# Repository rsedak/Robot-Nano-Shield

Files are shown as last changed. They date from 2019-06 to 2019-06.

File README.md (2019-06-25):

Introduction
============

Robot Nano Shield is Arduino Nano based shield for robots with dimentions compatibile with Lego(TM) liftarms.
For voltage stability L78S05CV Positive-Voltage regulator is used, and for power supply you can use two Li-Ion 18650 batteries.
During programming please keep in mind next design rules:
- D0-D1 — reserved for Bluetooth module (TX have onboard resistor voltage devider for HC-06 module)
- D2-D7 — reserved for H-bridge module (aka. L298N Dual H Bridge)
- D8 — reserved for servo motor
- D9-11 — reserved for RGB LED with onboard resistors
- D12-D13 — reserved for ultrasonic sensor HC-SR04
- A4-A5 — reserved for I2C communication with onboard pull-up resistors

Notice
------
Bluetooth module has to be disconnected during uploading a program to the Arduino Nano. 

Contributors
------------
- Petar Jurković had an idea for the shield with dimensions and features.
- Ines Sedak drew PCB back side picture.
- Robert Sedak did all design.

Application
-----------
Petar Jurković made video with Robot Nano Shield application in his robot:
Shield application (http://www.youtube.com/watch?v=B9CNlWZxvcw "Shield application")

Petar Jurković's Robot Nano Shield application
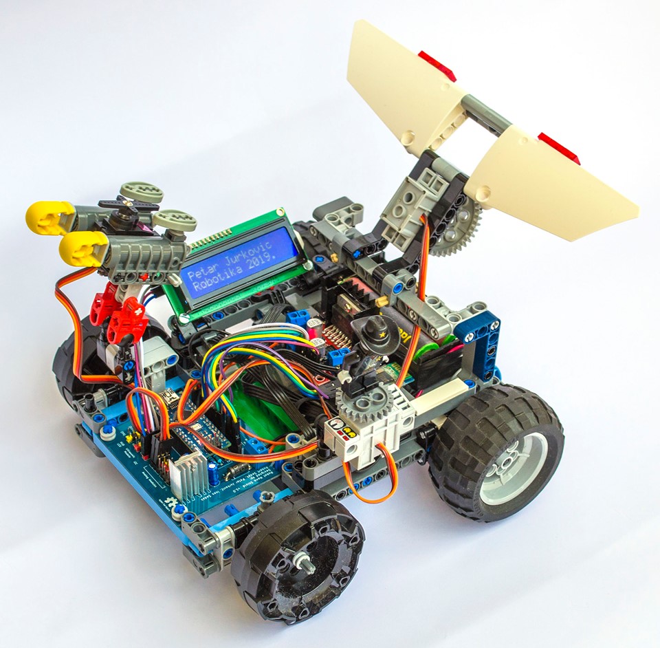
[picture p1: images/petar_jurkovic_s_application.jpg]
Robot Nano Shield Application
 

Bill Of Materials
-----------------
  
- 1 ea., PCB from [PCBway.com](https://www.pcbway.com/project/shareproject/Robot_Nano_Shield.html)
- 2 ea., 560 ohm 1/4W 1% Resistor (R2, R3)
- 2 ea., 1K ohm 1/4W 1% Resistor (R1, R4)
- 1 ea., 2K ohm 1/4W 1% Resistor (R5)
- 2 ea., 10K ohm 1/4W 1% Resistor (R6, R7)
- 1 ea., RGB LED 5mm common Katode (D1)
- 1 ea., 1N5400 Rectifier Diode (D2)
- 1 ea., L78S05CV Positive-Voltage regulator (U1)
- 1 ea., 10uF/25V Radial Aluminium Electrolytic Capacitor (C1)
- 1 ea., 220uF/10V Radial Aluminium Electrolytic Capacitor (C2)
- 1 ea., 2 Pin Plug-In Screw Terminal Block Connector 5.08mm Pitch
- 1 ea., 1x40Pin 2.54mm Straight Pin Header - Yellow
- 1 ea., 1x40Pin 2.54mm Straight Pin Header - Red
- 1 ea., 1x40Pin 2.54mm Straight Pin Header - Black
- 1 ea., 1x4 pin 2.54mm Socket Connector
- 2 ea., 1x15 pin 2.54mm Socket Connector
- 1 ea., Aluminum Heatsink Heat Sink with Screw Sets TO-220 Transistor 20×15×10mm

Design Files
------------
This project is designed using Open Source [KiCad](http://kicad-pcb.org/). Design files are located in the [design_files](design_files/) folder.  You can see the [schematic](images/robot_nano_shield_sch.png).

Firmware
--------
This project can be programed using the Open Source [Arduino](https://www.arduino.cc/).

Assembly Instructions
---------------------
TBD

License
-------
[Attribution-ShareAlike 3.0 United States (CC BY-SA 3.0 US)](https://creativecommons.org/licenses/by-sa/3.0/us/)

You are free to:
- Share — copy and redistribute the material in any medium or format
- Adapt — remix, transform, and build upon the material

This license is acceptable for Free Cultural Works.
- The licensor cannot revoke these freedoms as long as you follow the license terms.

Under the following terms:
- Attribution — You must give appropriate credit, provide a link to the license, and indicate if changes were made. You may do so in any reasonable manner, but not in any way that suggests the licensor endorses you or your use.
- ShareAlike — If you remix, transform, or build upon the material, you must distribute your contributions under the same license as the original.

No additional restrictions — You may not apply legal terms or technological measures that legally restrict others from doing anything the license permits.

Reference Designs ARE PROVIDED "AS IS" AND "WITH ALL FAULTS". Authors DISCLAIMS ALL OTHER WARRANTIES, EXPRESS OR IMPLIED,
REGARDING PRODUCTS, INCLUDING BUT NOT LIMITED TO, ANY IMPLIED WARRANTIES OF MERCHANTABILITY OR FITNESS FOR A PARTICULAR PURPOSE 
Authors may make changes to specifications and product descriptions at any time, without notice. The Customer must notrely on the absence or characteristics of any features or instructions marked "reserved" or "undefined." 
Authors reservesthese for future definition and shall have no responsibility whatsoever for conflicts or incompatibilities arising from future changes to them. The product information on the Web Site or Materials is subject to change without notice. Do not finalize a design with this info.

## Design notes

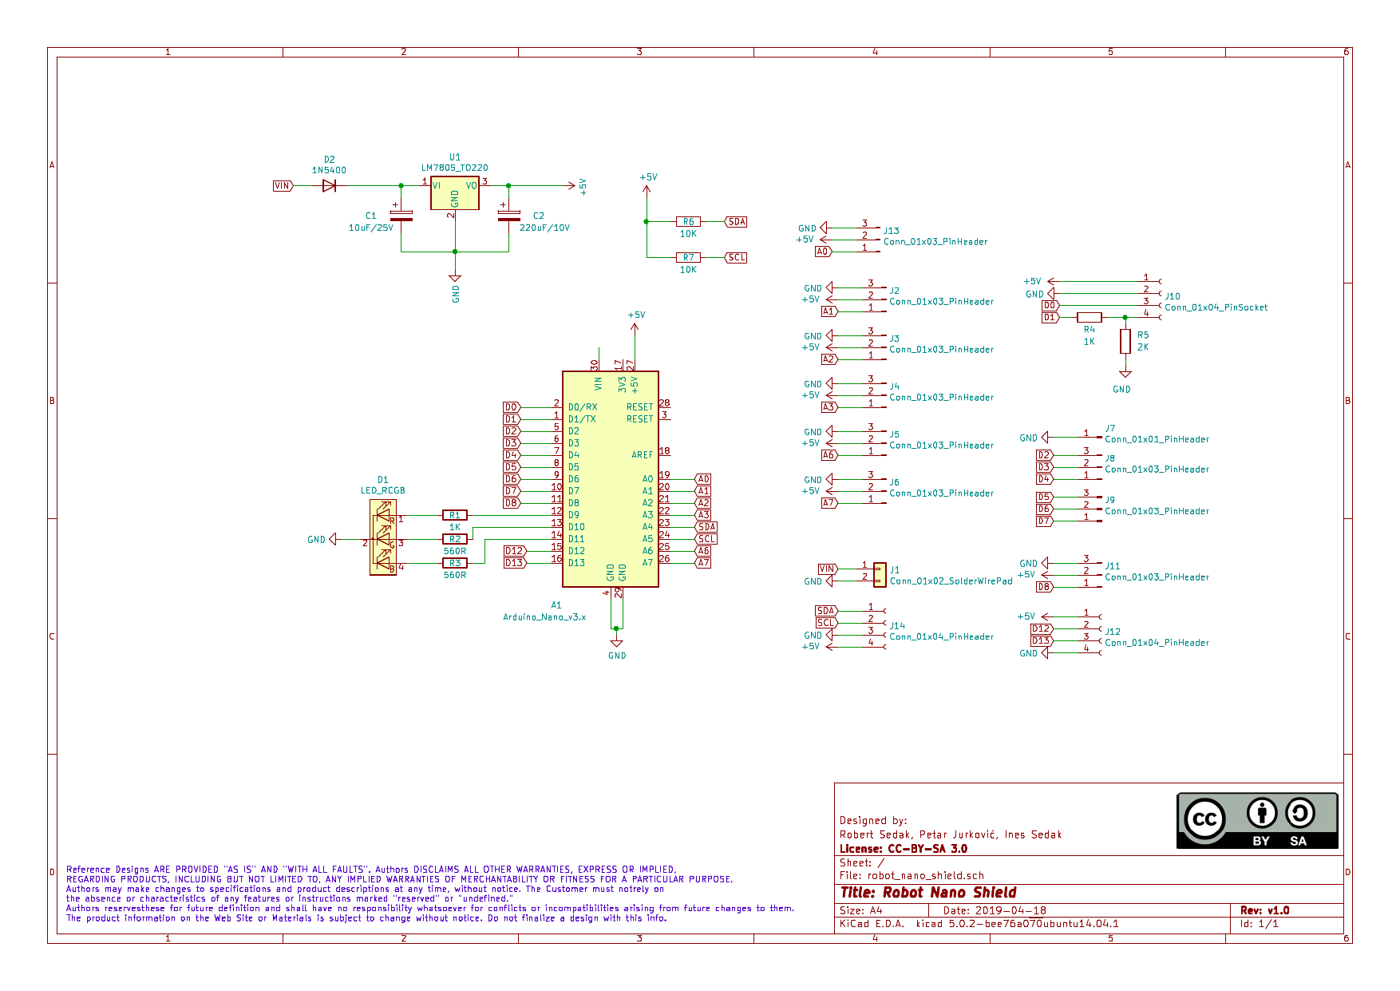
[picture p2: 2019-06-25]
images/robot_nano_shield_sch.png

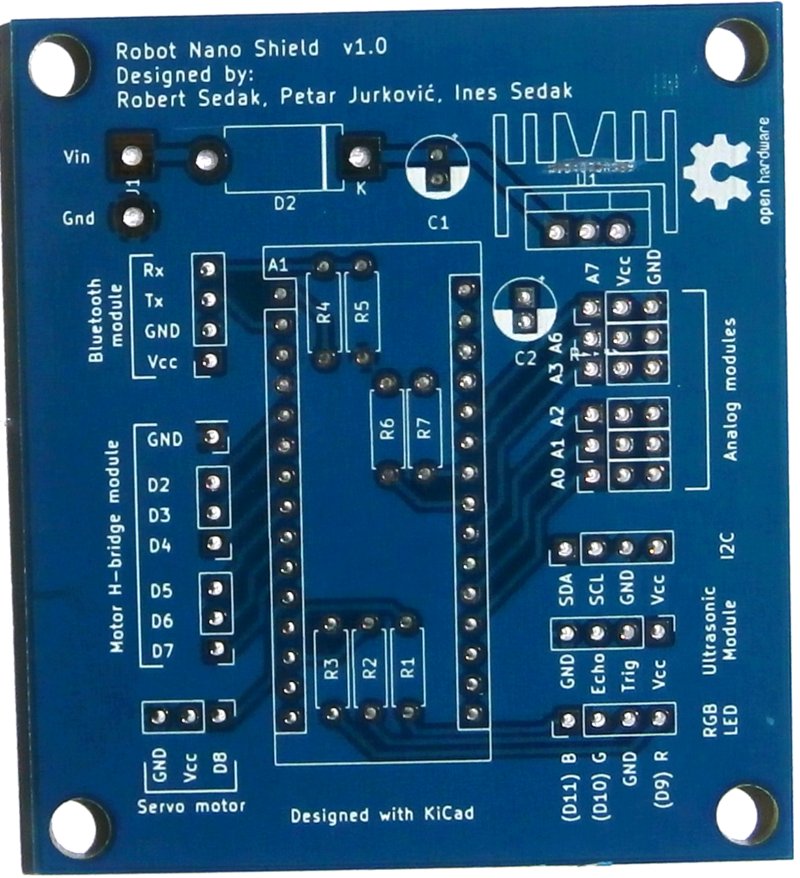
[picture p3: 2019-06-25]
images/robot_nano_shield_1.jpg

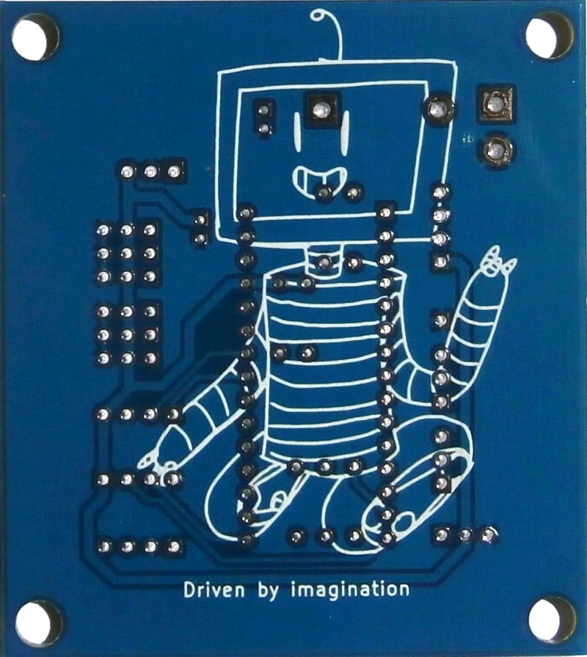
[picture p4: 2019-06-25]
images/robot_nano_shield_2.jpg

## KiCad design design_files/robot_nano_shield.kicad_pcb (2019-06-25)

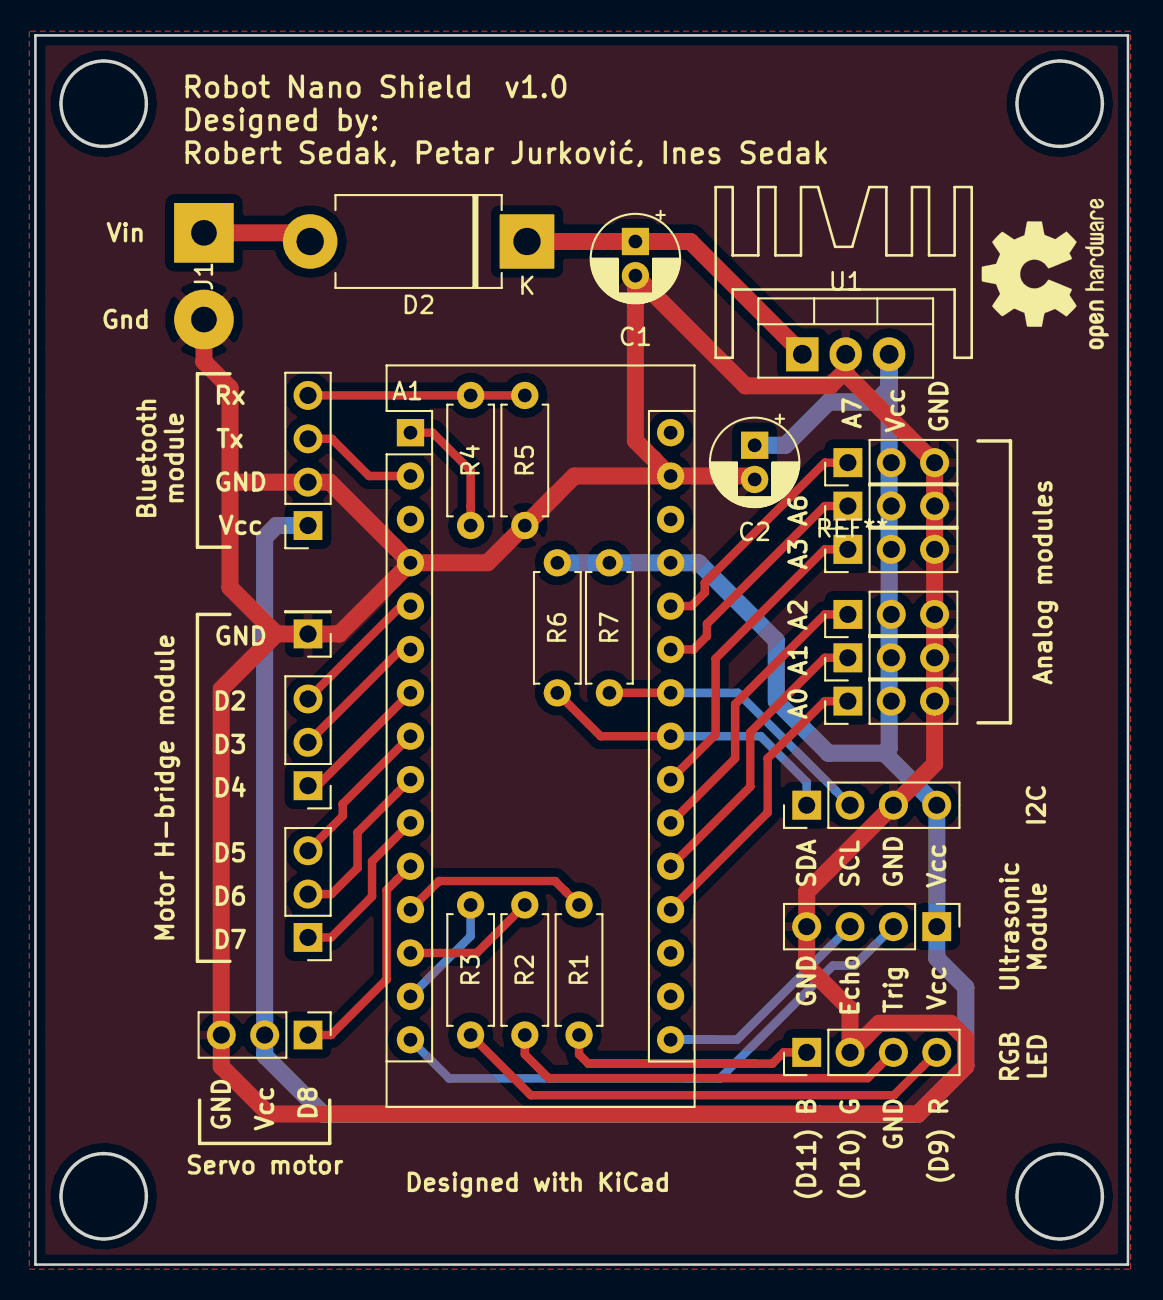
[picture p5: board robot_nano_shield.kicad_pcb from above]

Board: 2 copper layers, 64.0 x 72.0 mm, 27 parts (0 on the bottom side), 30 nets.

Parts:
A1: Arduino_Nano_v3.x; Arduino_Nano
C1: 10uF/25V; CP_Radial_D5.0mm_P2.00mm
C2: 220uF/10V; CP_Radial_D5.0mm_P2.00mm
D1: LED_RCGB; PinHeader_1x04_P2.54mm_Vertical
D2: 1N5400; D_DO-201AD_P12.70mm_Horizontal
J1: Conn_01x02; SolderWirePad_1x02_P5.08mm_Drill1.5mm
J2, J3, J4, J5, J6, J8, J9, J11, J13: Conn_01x03_Male; PinHeader_1x03_P2.54mm_Vertical
J7: Conn_01x01_Male; PinHeader_1x01_P2.54mm_Vertical
J10: Conn_01x04_Female; PinSocket_1x04_P2.54mm_Vertical
J12, J14: Conn_01x04_Female; PinHeader_1x04_P2.54mm_Vertical
R1, R4: 1K; R_Axial_DIN0207_L6.3mm_D2.5mm_P7.62mm_Horizontal
R2, R3: 560R; R_Axial_DIN0207_L6.3mm_D2.5mm_P7.62mm_Horizontal
R5: 2K; R_Axial_DIN0207_L6.3mm_D2.5mm_P7.62mm_Horizontal
R6, R7: 10K; R_Axial_DIN0207_L6.3mm_D2.5mm_P7.62mm_Horizontal
U1: LM7805_TO220; TO-220-3_Vertical

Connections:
+5V: A1.27, C2.1, J2.2, J3.2, J4.2, J5.2, J6.2, J10.1, J11.2, J12.1, J13.2, J14.4, R6.2, R7.2, U1.3
A0: A1.19, J13.1
A1: A1.20, J2.1
A2: A1.21, J3.1
A3: A1.22, J4.1
A6: A1.25, J5.1
A7: A1.26, J6.1
D0: A1.2, J10.3
D1: A1.1, R4.2
D2: A1.5, J8.3
D3: A1.6, J8.2
D4: A1.7, J8.1
D5: A1.8, J9.3
D6: A1.9, J9.2
D7: A1.10, J9.1
D8: A1.11, J11.1
D12: A1.15, J12.2
D13: A1.16, J12.3
GND: A1.4, A1.29, C1.2, C2.2, D1.2, J1.2, J2.3, J3.3, J4.3, J5.3, J6.3, J7.1, J10.2, J11.3, J12.4, J13.3, J14.3, R5.1, U1.2
unnamed: A1.12, R1.1
unnamed: A1.13, R2.1
unnamed: A1.14, R3.1
unnamed: C1.1, D2.1, U1.1
unnamed: D1.1, R1.2
unnamed: D1.3, R2.2
unnamed: D1.4, R3.2
unnamed: J10.4, R4.1, R5.2
SCL: A1.24, J14.2, R7.1
SDA: A1.23, J14.1, R6.1
VIN: D2.2, J1.1

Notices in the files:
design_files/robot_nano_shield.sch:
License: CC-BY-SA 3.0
